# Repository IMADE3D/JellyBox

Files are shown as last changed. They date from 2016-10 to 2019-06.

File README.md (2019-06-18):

| ⚠️ Warning: GitHub Mangles Zip Export ⚠️|
| --- |
|Do not download the project as a .zip if you want to use the 3mf Cura Project files. Github mangles the files and they will not work. Download the individual 3mf files from their pages or use git clone instead.|

# JellyBOX Files

Here you can find the JellyBox 3D Printer source files so you can **print spare parts**, or **modify the printer to your liking**!

## GCODE
- this is what you want it you want a **fast and easy spare part**
- **pre-sliced files ready to print** on your JellyBOX
- both cold and heated bed are fine
- depending on the filament and ambient temperature, heated bed is beneficial for some parts
- these are the gcodes we use for production
- well, we usually plate the parts many time (to print 16 clips at a time for example), but it's _equivalent gcode_

## STL
- STL files are the most common 3D exchange file
- pro: any slicer can process stl files
- con: stls are difficult to modify precisely - if you need to be changing the files, get STEP, IGES, or something like that...

## RLD
- rld files are used for laser cutting
- these are ready-to-lasercut

## State of the Art
- Update 2017-02-07
  - Several STLs and corresponding GCODEs have been updated. Left fan mount is re-inforced, feeder yoke and arm are smoother than ever, and there is a new mount for the flat proximity sensor without righ fan. Good things all around :cake: .
- Update 2016-11-21
  - GCODE, STL, RLD all published. The only parts missing are wire forms and native 3D files (step). We're working on it :-)
- Update 2016-10-01
  - JellyBox 1.3 is still in the stage of cleaning up the files. That's why you only find STLs here in the moment. Similarly, wire documentation is looking good, but it's not ready for public consumption. No worries; it's coming.

## License

  These files are licensed under *Creative Commons Attribution-NonCommercial-ShareAlike (CC BY-NC-SA 4.0)*. Read below and see “license.txt” more more information.

### Q: So is JellyBox open-source?
#### Contextual answer:
Yes!

We deeply and sincerely LOVE REMIX culture. We believe ideas are born out of other ideas, and being able to build on other people's projects is path to innovation. Similarly, we LOVE HACKING or, more specifically, making things do what we want the to do and modify them to suit our needs. Also, we LOVE REPAIRING our own devices.

Plus, we don't like to lock people into some sort of Orwellian proprietary system. After all, we are all children of RepRap. For all these reasons, we publish not only our production files (3D: stl and gcode, 2D: rld), but also source files that are way way easier to modify (3D: step).  We want you to play with the design! Make it better! See how it's done.

#### License specific answer:
CC BY-NC-SA 4.0 - now

We do love the remix culture, however, we do this for a living, and research and development of hardware AND of the build experience is incredibly arduous, resource intensive, and plainly expensive. We are building a network of licensed trainers and licensed manufacturers (Franchisees - interested? We strike good deals. Shoot us a message.), and we need to be able to guarantee our partners a competitive advantage at the beginning.

Thus, we publish the files under Creative Commons Attribution-NonCommercial-ShareAlike (CC BY-NC-SA 4.0) license. This allows anyone to print spare part to fix their printer, remix the parts, hack the heck out of it, even build a whole new project on top. Yet, this is not strictly Open-Source as the Open Source Hardware Association would tell you, but it is a common practice, it's within RepRap guidelines, and most people in fact do consider this open source. Even the original versions of GNU allowed non-commercial clause!

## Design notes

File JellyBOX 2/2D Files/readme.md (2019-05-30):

## File Formats

The master for geometry is an Illustrator file (.ai), but the master for production are Rdworks (.rld) files. The .ai files do _not_ contain all the informations, but only the shapes and colors. Line processing like dotted line, dashed line... is done in RDworks and is contained in the .rld files. 

If you can, we recommend you use RDworks with your laser. 

If you can't, then still try and download RDworks, and use the Preview function to see what all the settings do so you can replicate it in your laser host.

## Laser Control: Rdworks

You can find it here: http://www.rd-acs.com/down.aspx

RDcam/ RDworks is a Chinese piece of software that drives Ruida style lasercutting controllers. 

These are very common; known in the US as the ubiquitous 'Chinese lasercutters'.
Rdworks is a surprisingly capable piece of software. We use it to control our lasercutters. You can open the rdworks files, adjust the cutting settings to fit your laser (power/size) and get on cutting. 

Note that we run two passes on a regular high power CO2 laser. One is engraving - this one is run de-focused on purpose to get a wider and smoother engraving line. The second run is the cut - the black line. 

Get plastic covered acrylic if you can. Paper covered acrylic is more common, but the paper is a major pain to remove after the parts are cut. 
Leave the bottom protective sheet in place to mitigate burnup, but remove the top sheet to get a more predictable engraving. You may need to run active side fan while engraving to get less particle deposition. Also, air assist should be off for engraving (but definitely on for cutting!)

If you have access to an engraving machine, then feel free to use that, especially if you're only cutting one set or so!

PS: You can export geometry out of rdworks (ai, dxf) if you want to use other lasercutting controller. Just make sure to preview how all the dashed and dotted lines are rendered! This is done in rdworks, not in the geometry itself.

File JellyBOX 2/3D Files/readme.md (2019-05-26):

JellyBOX 3D printed parts are produced from PETG.

PETG is stringier and little worse behaved than PLA and demands a heated build plate, but it's mechanically superior and withstands higher temperatures. Warning: keep your PETG dry as it's hydrophilic and that destroys print strength. Look it up online if you don't know what we mean.

PLA will work for all of these parts most of the time, but you may need to print a repair more often as PLA is more brittle, less temperature resistant, and finally experiences creep under load. 

The few parts that really benefit from PETG even short term (not just long term or when in a hot car) are all the fan shrouds which are close to the hotend. 

The gcodes provided are sliced for PETG (!). Cura project files are included (.3mf). You can open these files and re-slice for another material (recommended) or export stl and slice differently altogether. Beware that many slices are optimized with very specific settings and modifier meshes. 

You could also do search and replace on the gcodes to make a workable pla gcode' see this discussion for more details
https://forum.imade3d.com/t/how-to-print-jellybox-parts-in-pla-and-not-petg/608

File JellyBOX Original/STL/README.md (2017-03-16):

## pink vs green
- if a filename has with "pink" - the part should be printed pink
- if a filename has with "green" - the part should be printed green

## STL
- STL files are the most common 3D exchange file
- pro: any slicer can process stl files
- con: stls are difficult to modify precisely - if you need to be changing the files, get STEP, IGES, or something like that...

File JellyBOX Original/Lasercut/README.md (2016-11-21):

## .rld files
- rld files are used for laser cutting
- these are ready-to-lasercut

## What is a "Cutform" ?
- Cutform is a part of our exquisite packaging efforts. Basically, a lasercut form core board to house specific parts and tools.
- Here's what it looks like:
-

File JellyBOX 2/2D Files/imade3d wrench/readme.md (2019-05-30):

## About the Wrench

We designed the IMADE3D wrench in house to have all the slots you need and not much more housed in sheer elegance. 
The wrench is laser cut from 3mm stainless steel.
The annotations are lasered in with a marking solution. 

## Laser Control: Rdworks

You can find it here: http://www.rd-acs.com/down.aspx

RDcam/ RDworks is a Chinese piece of software that drives Ruida style lasercutting controllers. 

These are very common; known in the US as the ubiquitous 'Chinese lasercutters'.
Rdworks is a surprisingly capable piece of software. We use it to control our lasercutters. You can open the rdworks files, adjust the cutting settings to fit your laser (power/size) and get on cutting. 

Note that we run two passes on a regular high power CO2 laser. One is engraving - this one is run de-focused on purpose to get a wider and smoother engraving line. The second run is the cut - the black line. 

Get plastic covered acrylic if you can. Paper covered acrylic is more common, but the paper is a major pain to remove after the parts are cut. 
Leave the bottom protective sheet in place to mitigate burnup, but remove the top sheet to get a more predictable engraving. You may need to run active side fan while engraving to get less particle deposition. Also, air assist should be off for engraving (but definitely on for cutting!)

If you have access to an engraving machine, then feel free to use that, especially if you're only cutting one set or so!

PS: You can export geometry out of rdworks (ai, dxf) if you want to use other lasercutting controller. Just make sure to preview how all the dashed and dotted lines are rendered! This is done in rdworks, not in the geometry itself.

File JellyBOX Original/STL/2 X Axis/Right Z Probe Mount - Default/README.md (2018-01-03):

## right z probe mount
- Mounts the Z Probe (proximity sensor) on the right side of the X Carriage.
- For flat and yellow z probe
- Also a part of the dual fan upgrade, but works stand alone as well.

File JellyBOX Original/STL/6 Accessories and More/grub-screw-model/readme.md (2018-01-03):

# About Grub Screw Model

- this part is made to demonstrate how the grub screw must go against the **flat** side of the motor shaft to properly _Grub_ it. 
- this is relevant to motor pulleys and the drive gear
- people have troubles seeing this concept because the grub screws are so tiny; hence this model. 

# Usage
- Print in PLA (perfectly fine) or PETG.
- ideally, each part would be different color of course 📗 📙 📕
- Use body-cut for testing the print settings and fit of the screw in the body - it's way faster to print
- you can play with flow, or, arguably better, simply uniformly resize by 1-2% as needed to adjust the tolerance between the parts
- the **collar is optional** - just glue it in to make the pulley even more realistic. good for Y - flushbess demonstration

# Screenshots




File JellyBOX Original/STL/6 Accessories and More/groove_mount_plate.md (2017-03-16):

## 3rd Party Groove Mount - Optional
This part is designed to hold 3rd party groove mount compatible hotend in the IMADE3D Extruder. (For example, you could fit a complete E3D V6 with its original fan assembly.)

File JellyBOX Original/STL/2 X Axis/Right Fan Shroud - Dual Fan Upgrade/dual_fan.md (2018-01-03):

## right fan shroud and right probe and fan mount

In JellyBOX 1.4, simply add the right fan shroud to the z probe mount. Done.

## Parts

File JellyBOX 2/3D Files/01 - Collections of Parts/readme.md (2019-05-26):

## Collections of Parts

These are designed to make one JellyBOX. If you print each plate once, you should be good. You can open the included Cura project (3mf.) file with Cura Imade3d Edition to print less or more parts. 

## Howto Print; PETG vs PLA

JellyBOX 3D printed parts are produced from PETG.

PETG is stringier and little worse behaved than PLA and demands a heated build plate, but it's mechanically superior and withstands higher temperatures. Warning: keep your PETG dry as it's hydrophilic and that destroys print strength. Look it up online if you don't know what we mean.

PLA will work for all of these parts most of the time, but you may need to print a repair more often as PLA is more brittle, less temperature resistant, and finally experiences creep under load. 

The few parts that really benefit from PETG even short term (not just long term or when in a hot car) are all the fan shrouds which are close to the hotend. 

The gcodes provided are sliced for PETG (!). Cura project files are included (.3mf). You can open these files and re-slice for another material (recommended) or export stl and slice differently altogether. Beware that many slices are optimized with very specific settings and modifier meshes. 

You could also do search and replace on the gcodes to make a workable pla gcode' see this discussion for more details
https://forum.imade3d.com/t/how-to-print-jellybox-parts-in-pla-and-not-petg/608

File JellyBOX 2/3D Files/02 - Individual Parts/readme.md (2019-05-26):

## My Part is Not Here?!

If you can't find the part you're looking for, plase go to the "Collections of Parts" folder, open the appropriate .3mf file with Cura Imade3d Edition, and simply delete everything you don't need and reslice. You shall not be stopped!

## Howto Print; PETG vs PLA

JellyBOX 3D printed parts are produced from PETG.

PETG is stringier and little worse behaved than PLA and demands a heated build plate, but it's mechanically superior and withstands higher temperatures. Warning: keep your PETG dry as it's hydrophilic and that destroys print strength. Look it up online if you don't know what we mean.

PLA will work for all of these parts most of the time, but you may need to print a repair more often as PLA is more brittle, less temperature resistant, and finally experiences creep under load. 

The few parts that really benefit from PETG even short term (not just long term or when in a hot car) are all the fan shrouds which are close to the hotend. 

The gcodes provided are sliced for PETG (!). Cura project files are included (.3mf). You can open these files and re-slice for another material (recommended) or export stl and slice differently altogether. Beware that many slices are optimized with very specific settings and modifier meshes. 

You could also do search and replace on the gcodes to make a workable pla gcode' see this discussion for more details
https://forum.imade3d.com/t/how-to-print-jellybox-parts-in-pla-and-not-petg/608

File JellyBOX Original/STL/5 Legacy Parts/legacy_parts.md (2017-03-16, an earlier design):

## filament guide 2.0 green
This filament guide was used for JellyBOX 1.2 with two spool rollers on the top.

## Extruder with `9` mm Drive Gear
### extruder 9mm 1.2 pink
As mentioned, use this extruder base if your drive gear has an effective diameter of ___ mm. In Spring of 2017, we have switched our production to drive gear with ___ mm . Then smaller drive gear exerts more force, but the older one works perfectly fine. No dire need to upgrade.

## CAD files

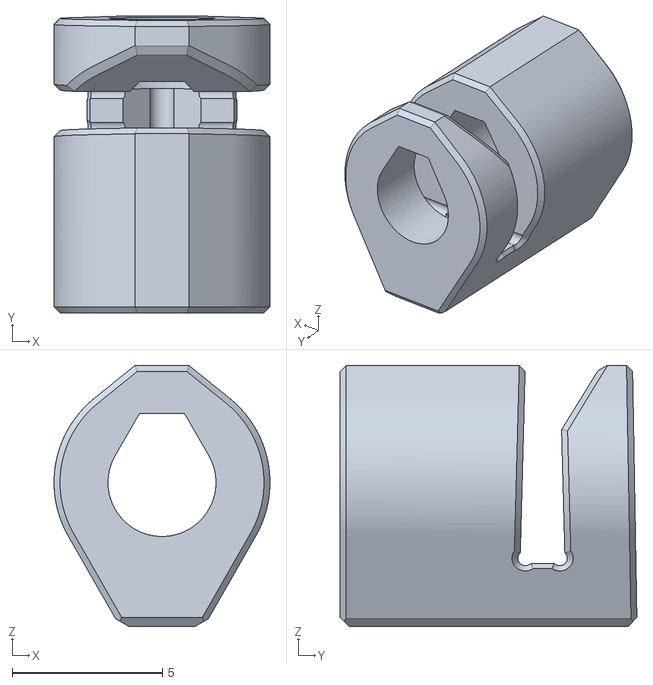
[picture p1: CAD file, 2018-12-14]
JellyBOX 2.1.b to 2.1.b.b upgrade/LCD spacer/LCD-spacer-beefy.stl
7.20 x 9.89 x 8.70

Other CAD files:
JellyBOX 2.1.b to 2.1.b.b upgrade/Corner clip without ends/corner clip body without ends @1 petg.3mf
JellyBOX 2/3D Files/01 - Collections of Parts/01A - pink/pink.3mf
JellyBOX 2/3D Files/01 - Collections of Parts/01B - pink with fixed position z probe/pink.3mf
JellyBOX 2/3D Files/01 - Collections of Parts/02 - pink extruder/pink extruder.3mf
JellyBOX 2/3D Files/01 - Collections of Parts/03 - green 0.2/green 0.2.3mf
JellyBOX 2/3D Files/01 - Collections of Parts/04 - green 0.3/green 0.3.3mf
JellyBOX 2/3D Files/01 - Collections of Parts/05 - idler flange/x1 idler flange.3mf
JellyBOX 2/3D Files/01 - Collections of Parts/06 - x carriage/x carriage.3mf
JellyBOX 2/3D Files/01 - Collections of Parts/07 - filament fan shrouds/x1 filament fan shrouds.3mf
JellyBOX 2/3D Files/01 - Collections of Parts/08 - hotend fan cover/x1 hotend fan cover cura.3mf
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

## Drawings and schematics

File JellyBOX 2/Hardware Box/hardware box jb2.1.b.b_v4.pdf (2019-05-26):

### M3 plastite screw

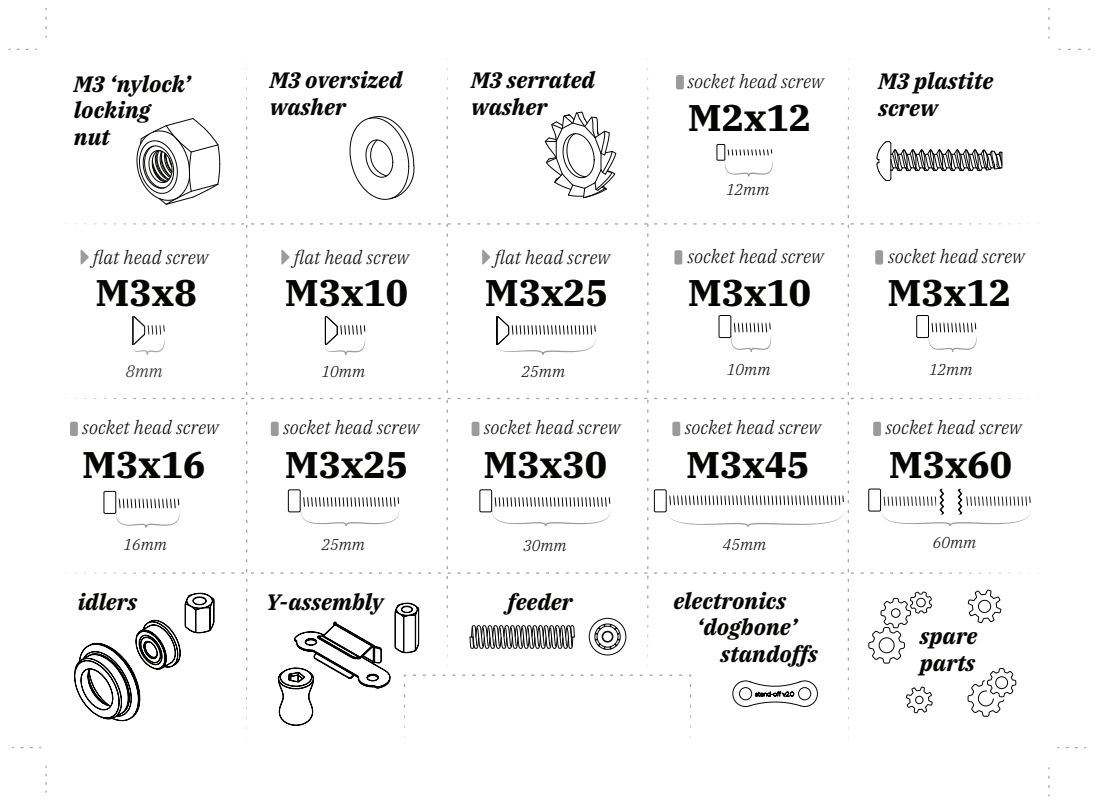
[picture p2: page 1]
M3 serrated washer; spare parts; M3 oversized washer; M3 ‘nylock’ locking nut; idlers; Y-assembly; feeder; electronics; ‘dogbone’ standoffs; socket head screw; flat head screw

socket head screw

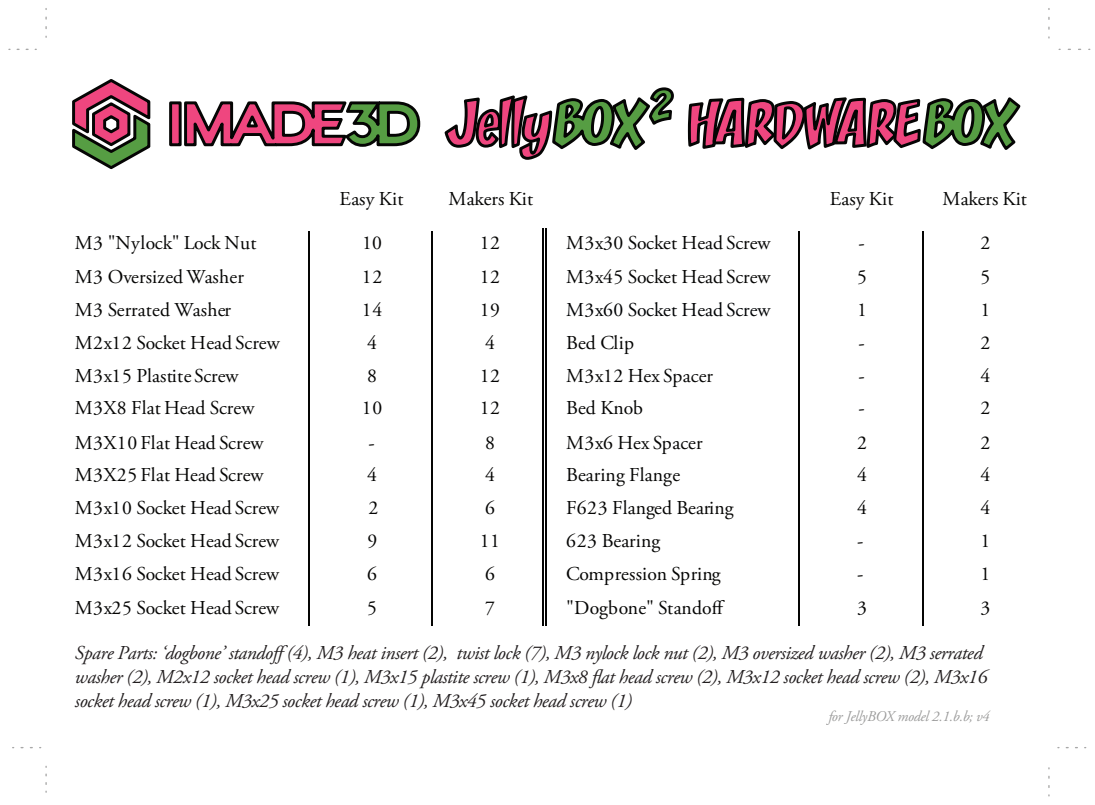
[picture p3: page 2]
Easy Kit; Makers Kit; M3 "Nylock" Lock Nut; M3x30 Socket Head Screw; M3 OversizedWasher; M3x45 Socket Head Screw; M3 Serrated Washer; M3x60 Socket Head Screw; M2x12 Socket Head Screw; Bed Clip; M3x15 Plastite Screw; M3x12 Hex Spacer; M3X8 Flat Head Screw; Bed Knob; M3X10 Flat Head Screw; M3x6 Hex Spacer; M3X25 Flat Head Screw; Bearing Flange; M3x10 Socket Head Screw; F623 Flanged Bearing; M3x12 Socket Head Screw; 623 Bearing; M3x16 Socket Head Screw; Compression Spring; M3x25 Socket Head Screw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

Spare Parts: ‘dogbone’ stando (4), M3 heat insert (2), twist lock (7), M3 nylock lock nut (2), M3 oversized washer (2), M3 serrated
washer (2), M2x12 socket head screw (1), M3x15 plastite screw (1), M3x8 at head screw (2), M3x12 socket head screw (2), M3x16
socket head screw (1), M3x25 socket head screw (1), M3x45 socket head screw (1)

for JellyBOX model 2.1.b.b; v4

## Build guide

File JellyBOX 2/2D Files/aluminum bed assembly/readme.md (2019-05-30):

## About the bed assembly

These parts are cut form 3mm aluminum. Make sure not to heat-warp the parts when cutting! You may need to straighten them. These should be as flat as possible.

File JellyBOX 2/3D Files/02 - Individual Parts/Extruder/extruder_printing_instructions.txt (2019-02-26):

This file is pre-sliced for PETG on a JellyBOX Original or 2.

To print in other materials, use the open the included 3mf Cura project file in the latest Cura IMADE3D Edition (go.imade3d.com/cura-download) and edit the settings to your liking. 

Alternatively, open the gcode in text editor and change the temperatures...

You can also slice the stl yourself, but beware that this file uses advanced techniques (local override of inner settings) to get a locally stronger print.

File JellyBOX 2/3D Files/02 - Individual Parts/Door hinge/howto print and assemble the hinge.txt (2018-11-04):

We print these from PETG. 

Use 3 perimeters around the hinge part itself to achieve maximum stiffness. Depending on your extruderÕs calibration, you may also need to tweak the flow to achieve a tight fit. 

We use a piece of 1.75mm PETG filament as the hinge pin!

1. Heat up something to 100 ¡C or more. Touch one end of a piece of filament to it so it melts and creates a little plug at the end. use a piece of metal (your IMADE3D wrench for example) to smoothen the plug. 
2. Insert into the hinge. 
3. Trim the filament so that about 2mm are sticking out. 
4. Melt and squash the other side of the filament to seal the pin in the hinge. 
5. Tadaaa.

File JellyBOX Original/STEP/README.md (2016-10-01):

Still cleaning up the step files. If you need a specific part, email at info@imade3d.com

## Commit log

2016-10-01 sth initial commit
    sth files with no explanation for now :-)
    [g QR c clamp 4.5.stl, g arm 1.2.stl, g clip 1.0.stl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]
2016-10-02 2 year period out
    until partnership agreements finalize it’s too irresponsible to promise
    future licensing options. we still hope for the original plan, but
    better to be safe than sorry.
2016-11-21 Add lasercut .rld files
    Changed location of Cutform folder - move under lasercut/Jellybox1.3
    folder
    Add .rld lasercut files to same folder.
2016-11-21 update STL readme
2017-02-06 update feeder arm & yoke for vertical printing
    The feeder arm and the feeder yoke were both modiffied to be printed
    vertically. The result is a smoother movement of the yoke - that is
    easier to print.
    [g arm 1.2.stl, p yoke 1.2.stl]
2017-02-06 Update gcodes for vertically printer arm and yoke
    Gcodes for updated vertically printed arm and yoke. PLA, 210C,
    resolution 0.2mm. Arm gcode is generated with support.
2017-02-06 center the feeder arm on the build plate .stl
    the feeder arm was way off the build center for some reason, but no
    more! rejoice.
    [g arm 1.2.stl]
2017-02-07 bump arm and yoke version number
    we forgot to bump the version number, even though these have been
    significantly redesigned.
    [g arm 2.0.stl, p yoke 2.0.stl]
2017-02-07 rename the filament fan shroud mounts (L & R) for easier sorting
    now they will show next to the fan shrouds, and next to each other.
    [p fan shroud mount L 1.4.stl, p fan shroud mount R and flat proximity sensor 1.2.stl]
2017-02-07 reinforce the left fan mount
    the slot has been made shorter by 3mm, which in turn makes the part
    stronger. we have had numerous report of people breaking this part when
    getting too liberal with their tightening of the mounting screws. this
    reinforcement should prevent mishaps.
    [p fan shroud mount L 1.4.stl]
2017-02-07 bump up the version number of left fan mount
    [p fan shroud mount L 1.5.stl]
2017-02-09 describe late updates in stl department in readme
    that is, root readme.md
2017-02-17 add flat probe mount with no fan
    Normally, the right fan shroud mount and the flat probe mount are one
    and single piece. This model allows to mount the yellow flat probe with
    no fan on the right side, thus keeping up a single left fan
    configuration.
    [p flat probe mount 2.1.stl]
2017-02-17 rename the flat probe and right fan mount
    to correspond better with the new probe mount with no fan on the right
    side (p flat probe mount 2.1)
    [p flat probe mount and fan shroud mount R 1.2.stl]
2017-02-17 rotate the flat proble and fan shroud mount
    this corresponds to the way it should be printed.
    [p flat probe mount and fan shroud mount R 1.2.stl]
2017-02-21 replace filement guide with correct stl
    the stl for the shorter filament guide in the center of the jellybox
    since V1.3 was a wrong file. it’s good now.
    [g filament guide 1.3 dev 1.stl, g filament guide 3.0.stl]
2017-02-26 rotate the hotend shroud
    [g hotend shroud 1.1.stl]
2017-03-16 rename and reorganize files
    the stl files have been heavily reorganized into subfolders.
    they have also been updated and rotated in the orientation ready to be sliced.
    [clamp cut 4.5.1 green.stl, corner clip 1.0 green.stl, ear.stl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]
2017-03-16 resolve merge conflicts
    [g hotend shroud 1.1.stl]
2017-04-10 add extruder fan cover
    where was it hiding? noone knows.
    note that this is the thick plastite/taptite version - backwards
    compatible with all other versions.
    [fan cover green.stl]
2017-04-14 initial commit model of motor shaft
    [body-cut.stl, body.stl, motor-shaft.stl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]
2017-04-14 tweak body and add speedier test print
    [body-cut.stl, body.stl]
2017-04-14 make the body look more like an actual pulley
    this way we can demonstrate how to tighten the X and Y pulleys -
    specifically the gap for X pulley…
    [body.stl]
2017-04-14 add optional collar - to be glued in
    [collar.stl]
2017-07-07 replace the 9mm legacy extruder plate with 8mm ed
    geometry is the same, but the annotation differs, and the naming is
    consistent with the default 7mm ed now.
    [extruder 8mm-ed pink.stl, extruder 9mm 1.2 pink.stl]
2018-01-03 organize the STL files. - rename to get rid of confusing numbers. - align with internal structure
    [clamp cut 4.5.1 green.stl, corner clip green.stl, extruder 7mm-ed pink.stl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]
2018-01-03 add x carriage and extruder gcodes that were missing!
2018-01-03 add missing extruder and xcarriage gcodes
2018-08-03 add part scraper stl, 3mf, and gcodes
    [scraper.3mf, scraper.stl]
2018-11-04 Split folders into JellyBOX Original and JellyBOX 2
    [body-cut.stl, body.stl, collar.stl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]
2018-11-04 Add door hinge gcode, stl, and txt howto
    [door hinge.stl]
2018-11-21 Add z probe mount files
    - stl, gcode, 3mf
    - this is the newest one, with improved probe angle
    [z probe mount slot.stl, z probe mount slot@1.3mf]
2018-12-03 Add JellyBOX 2 left fan mount stl, 3mf, gcode
    [left fan mount slot.3mf, left fan mount.stl]
2018-12-14 Add JellyBOX 2.1.b to 2.1.b.b Upgrade folder
    [LCD-spacer-beefy.stl, LCD-spacer-beefy@23.3mf, corner clip body without ends @1 petg.3mf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]
2019-02-26 Organize JellyBOX 2 files
    [door hinge.stl]
2019-02-26 Add Extruder
    - re-sliced with JellyBOX 2 in cura 3.5.1
    [01 B - pink extruder.3mf, 01 B - pink extruder.stl]
2019-02-27 Add cutting edge Z Probe mount files
    - the slot version
    - the fixed position one hole version, beta2
    [z probe additional walls.stl, z probe fixed position - M3 nut - beta2.stl, z probe fixed position - heat inserts - beta2.3mf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]
2019-04-01 Add idler flange
    3mf and gcode
    [idler flange.3mf]
2019-05-26 Add 3mf and stl to lfs (what a title :-) )
2019-05-26 Reorganize the JellyBOX 2 3D files
    [01 B - pink extruder.3mf, 01 B - pink extruder.stl, LCD-spacer-beefy.stl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]
2019-05-26 Git is refreshing because of lfs
    [LCD-spacer-beefy.stl, LCD-spacer-beefy@23.3mf, corner clip body without ends @1 petg.3mf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]
2019-05-26 Add the JellyBOX 2D files, for lasercutting
2019-05-30 Add aluminum parts to the release
    - build plate and bed assembly base
2019-06-28 Re-orient the Z probe spacer
    [z probe spacer 1mm.stl, z probe spacer@10.3mf]
2020-01-09 Clarify names of files/ folders
    [x1 hotend fan cover cura.3mf]
2020-01-09 Add individual L / R fan shrouds gcodes
    [x1 filament fan shrouds.3mf]
